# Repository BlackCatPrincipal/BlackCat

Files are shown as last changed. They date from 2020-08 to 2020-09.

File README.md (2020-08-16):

# BlackCat

Black Cat is a 3D printer project to build a fully open source 3D printed UM2 printer, and most of the components are 3D printed.

This repository contains DWG and DXF for laser cut parts, STP files and STLs for the printed parts.

Open Source with the help of [southern-dust](https://github.com/southern-dust).

#### 中文说明

BlackCat 自主设计完全开源3D打印的UM2打印机，大部分部件采用3D打印件。

这个 repo 包含用于激光切割零件的DWG和DXF文件，以及用于3D打印零件的STP和STL文件。

在 [southern-dust](https://github.com/southern-dust) 的帮助下开源。

特别的，提供作者QQ群：713105644，欢迎来交流讨论。

## License

The content of this project itself is licensed under the [Creative Commons Attribution 3.0 Unported license](https://creativecommons.org/licenses/by/3.0/), and the underlying source code used to format and display that content is licensed under the [MIT license](https://github.com/github/choosealicense.com/blob/gh-pages/LICENSE.md).

## 许可证

该项目本身的内容已根据 [Creative Commons Attribution 3.0 Unported license](https://creativecommons.org/licenses/by/3.0/) 进行了许可，用于格式化和显示该内容的基础源代码也以 [MIT license](https://github.com/github/choosealicense.com/blob/gh-pages/LICENSE.md) 进行了许可。

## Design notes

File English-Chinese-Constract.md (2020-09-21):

#### 中英文对照 English-Chinese filename constrast

##### cad(the DXF folder is the same content, but using the DXF open file format)

| Englinsh | 中文 |
| :---: | :---: |
| bottomPlate | 底板 |
| middlePlate | 中板 |
| platformBottomPlate | 平台底板 |
|  platformTopPlate | 平台上板 |

##### stl

| Englinsh | 中文 |
| :---: | :---: |
| bottomPlate | 底盘 |
| topPlate | 上盖 |
| back-Pillar | 立柱1 |
| front-Pillar | 立柱2 |
| e3d-Holder-Back | e3d支架1 |
| e3d-Holder-Front | e3d支架2 |
| Z-Carrige | z平台滑块 |
| Z-Support |  z平台三角支架  |
| Z-Shaft-Idler-10mm | z轴10mm光轴挡板 |
| Z-Endstop-Mount |  z限位固定支座  |
| motor-Spacer | 电机支架 |
| shaftBearing-Belt-holder | 直线轴承同步带  |
| PartCoolingFanMount | 风扇支架 |

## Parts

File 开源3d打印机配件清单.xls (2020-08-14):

编号 | 名称 | 规格 | 单位 | 数量 | 单价 | 总价
1 | 打印件 | 机箱外壳 | g | 1000 |  |  | Printed Parts
2 | 主板 | 创客基地MKS.Gen_L V1.0加屏幕 | 个 | 1 | 144 | 144 | Motherboard |  | 1
3 | 电机 | 42*40步进电机 | 个 | 3 | 26 | 78 | NEMA 17 Steppers | 42*40 | 3
4 | 电机 | 42*34步进电机 | 个 | 1 | 13.5 | 13.5 | NEMA 17 Steppers | 42*34 | 1 | Used for extruder?
5 | 喷头 | E3DV6 | 个 | 1 | 18 | 18 | Extruder | E3DV6 | 1
6 | 亚克力 | 285*285mm | 个 | 1 | 15 | 15 | Lasercut | 285*285mm | 1
7 | 亚克力 | 275*275mm | 个 | 1 | 15 | 15 | Lasercut | 275*275mm | 1
8 | 亚克力 | 170*180mm | 个 | 2 | 10 | 20 | Lasercut | 170*180mm | 2
9 | 限位开关 | Ultimaker2限位开关长脚 | 个 | 3 | 3 | 9 | Endstop | Mechanical Endstop | 3
10 | z轴光轴 | Φ10*320 | 根 | 2 | 7.5 | 15 | Z axis Shafts | Φ10*320 | 2
11 | x轴光轴 | Φ8*270 | 根 | 2 | 6 | 12 | X axis Shafts | Φ8*270 | 2
12 | y轴光轴 | Φ8*285 | 根 | 2 | 6 | 12 | Y axis Shafts | Φ8*285 | 2
13 | x轴十字轴 | Φ6*240 | 根 | 1 | 4.5 | 4.5 | X axis Center Shafts | Φ6*240 | 1
14 | y轴十字轴 | Φ6*225 | 根 | 1 | 4.5 | 4.5 | Y axis Center Shafts | Φ6*225 | 1
15 | 直线法兰轴承 | Φ10 | 个 | 2 | 8.45 | 16.9 | Z Shaft Flange Bearing | Φ10 | 2
16 | 散热风扇 | 30mm*30mm | 个 | 1 | 4 | 4 | fan | 30mm*30mm | 1
17 | 尼龙垫柱 | 8*2 | 个 | 8 | 0.15 | 1.2
18 | 尼龙垫柱 | 8*5 | 个 | 7 | 0.08 | 0.56
19 | 同步轮 | 2GT-20-6 | 个 | 2 | 5 | 10 | GT2 Pulley | 2GT-20-6 | 2
20 | 同步轮 | 2GT-20-8 | 个 | 8 | 7 | 56 | GT2 Pulley | 2GT-20-8 | 8
21 | 同步轮 | 2GT-20-8双头 | 个 | 1 | 9.5 | 9.5 | GT2 Pulley | 2GT-20-8 2sides | 1
22 | 弹簧 | Φ8*15 | 个 | 4 | 0.8 | 3.2
23 | 联轴器 | Φ6转Φ8铝合金联轴器 | 个 | 1 | 1.1 | 1.1 | Z Coupler | Φ6toΦ8 | 1
24 | 丝杆 | 8*270mm | 个 | 1 | 10 | 10 | Z Leadscrew/nut | 8*270mm
25 | 同步带 | 2GT闭环同步带500mm | 个 | 2 | 11.66 | 23.32 | GT2 Belt | 500mm | 1
26 | 开关 | 20mm船型开关 | 个 | 1 | 2.1 | 2.1 | Power Switch | 20mm | 1
27 | 轴承 | f688zz | 个 | 8 | 2.5 | 20 | Bearing | f688zz | 8
28 | 同步带 | 2GT同步带450mm | 个 | 4 | 1.2 | 4.8 | GT2 Belt | 450mm | 4
29 | 电源 | 5.5mmDC直流插头母头 | 个 | 1 | 3.2 | 3.2 | Power Supply
30 | 挤出机 | 泰坦远程挤出机 | 个 | 1 | 21 | 21 | Extruder | Titan remote | 1
31 | 直线轴承 | LM8UU | 个 | 4 | 2 | 8 | Shaft Bearing | LM8UU | 4
32 | 调平螺母 | m3蝶形螺母 | 个 | 4 | 1.3 | 5.2 | Nuts | M3 | 4
33 | 直线轴承 | LM6LUU | 个 | 2 | 5.5 | 11 | Shaft Bearing | LM6LUU | 2
 |  |  |  |  |  | 571.58
清单仅供参考

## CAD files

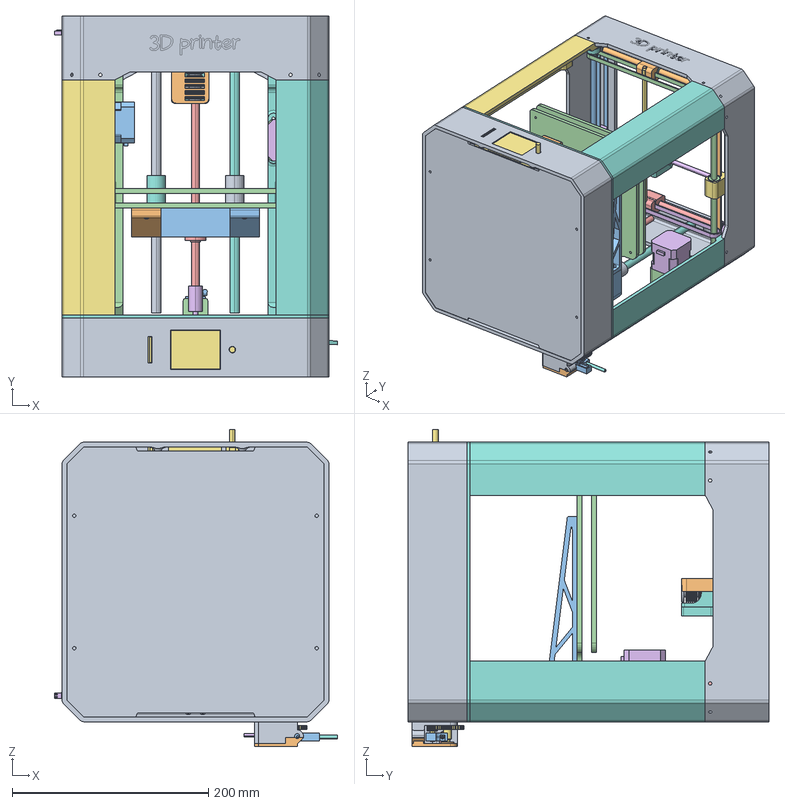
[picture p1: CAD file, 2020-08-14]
BlackCat.FCStd
288.5 x 368.0 x 323.2 mm
topPlate
GT2-Belt001
NEMA17Steppers001
back-Pillar001
GT2-Belt002
NEMA17Steppers002
front-Pillar001
front-Pillar002
bottomPlate
X-Shaft8mm001
Y-Shaft8mm001
Y-Shaft8mm002
X-Shaft8mm002
X-CenterShaftsΦ6*240
Y-CenterShaftsΦ6*225
e3d-Holder-Back
e3d-v6-hotend
e3d-Holder-Front
Z-Carrige
Y-Endstop
f688zz008
X-Endstop
LCD-SmartController
lmk10mm0002
lmk10mm001
Z-Support001
Z-Support002
platformBottomPlate
GT2-Pulley20mm001
GT2-Pulley20mm002
f688zz001
f688zz002
f688zz003
f688zz004
f688zz005
f688zz006
f688zz007
GT2-Pulley20mm003
GT2-Pulley20mm004
GT2-Pulley20mm005
GT2-Pulley20mm006
GT2-Belt450mm003
GT2-Belt450mm001
GT2-Belt450mm002
2GT-20-8 2sides
NEMA17Steppers004
NEMA17Steppers003
Z-Shaft10mm001
Z-Shaft10mm002
Z-Screw
Z-Endstop
Z-Endstop-Mount
Z-LeadscrewT8*270mm
GT2-Belt450mm004
GT2-Pulley20mm007
back-Pillar002
bottomPlate001
shaftBearing-Belt-holder004
LM6LUU002
LM8UU004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

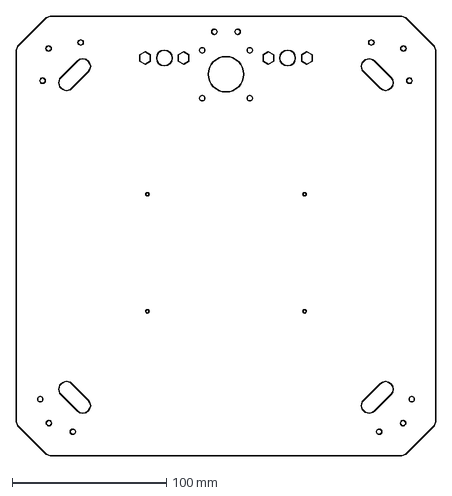
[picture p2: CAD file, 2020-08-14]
Lasercut/DXF/中板.dxf
272.0 x 285.0 mm

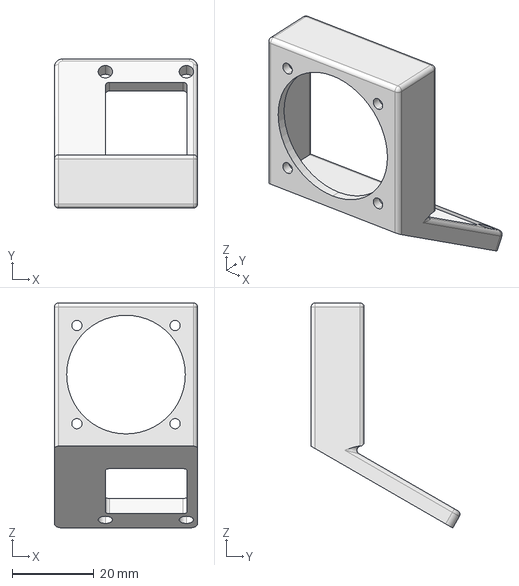
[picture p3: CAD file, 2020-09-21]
Printed-Parts/PartCoolingFanMount.FCStd
35.0 x 36.4 x 55.0 mm

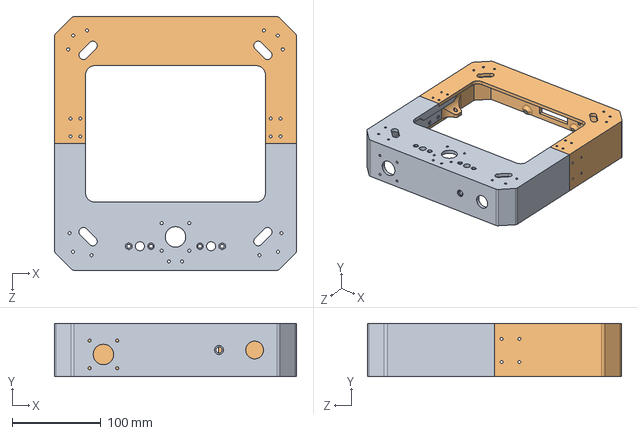
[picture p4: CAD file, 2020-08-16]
Printed-Parts/step/bottomPlate-split.step
272.0 x 60.0 x 285.0 mm
菁攫1
菁攫2

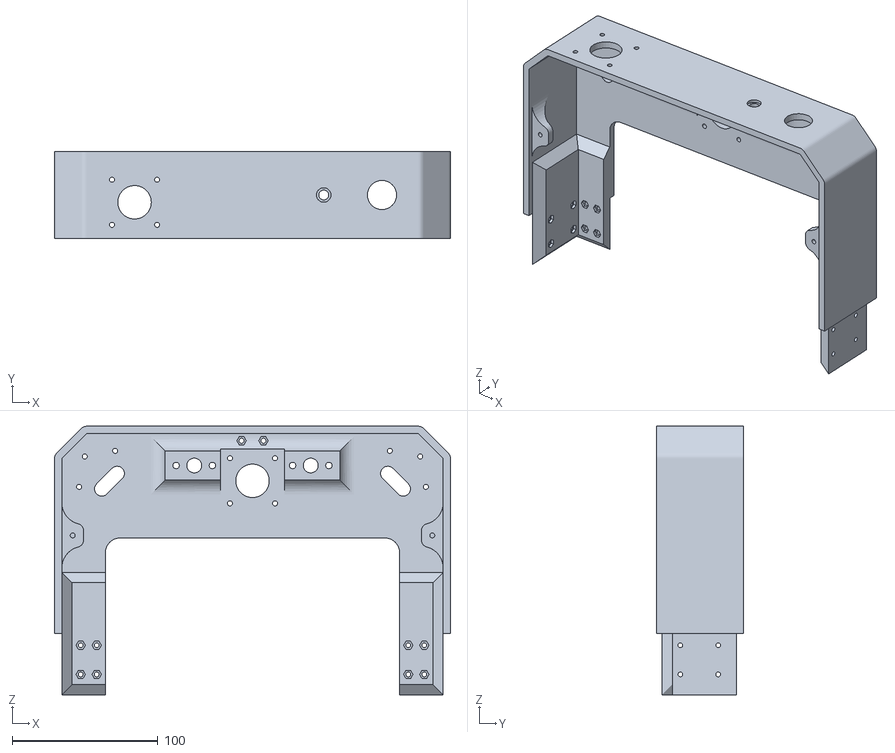
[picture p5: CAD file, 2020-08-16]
Printed-Parts/stl/bottomPlate-split-back.STL
272.0 x 60.0 x 184.5

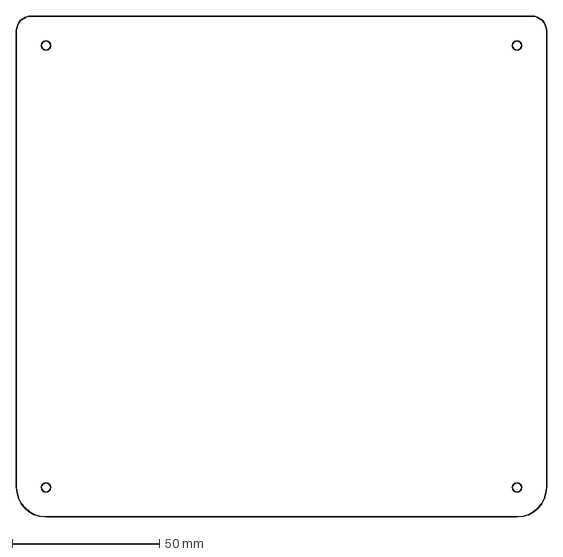
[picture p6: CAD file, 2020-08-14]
Lasercut/DXF/平台上板.dxf
180.0 x 170.0 mm

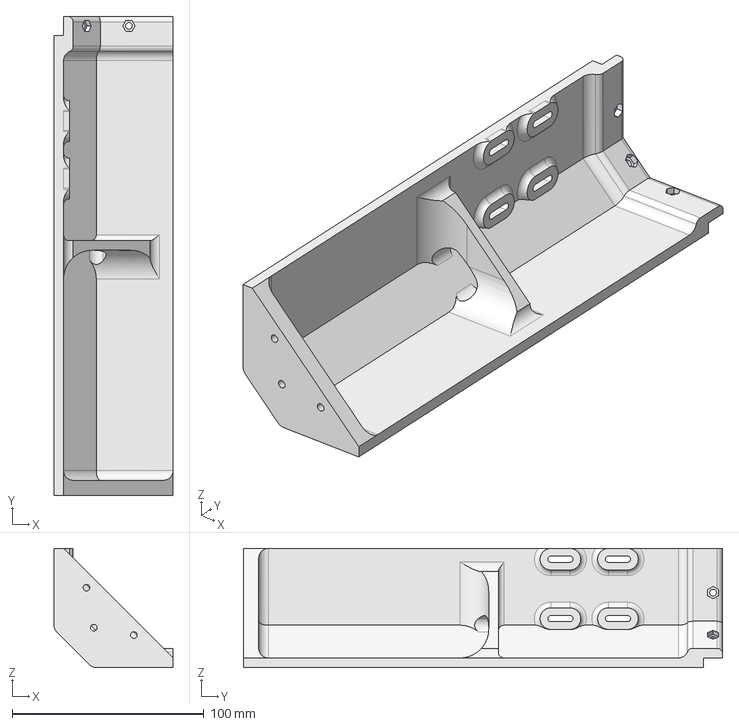
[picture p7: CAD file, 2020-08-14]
Printed-Parts/step/back-Pillar.step
62.1 x 250.0 x 62.1 mm

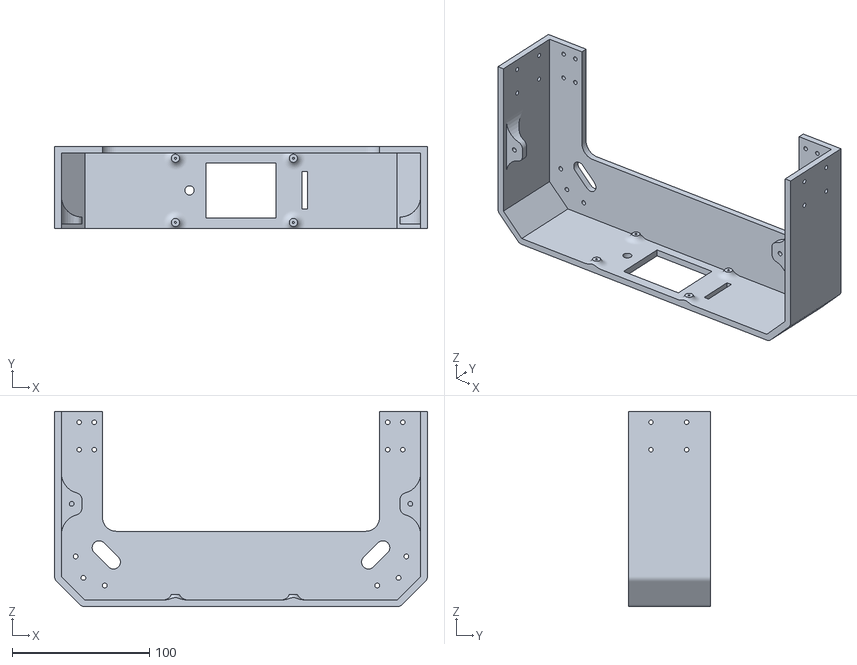
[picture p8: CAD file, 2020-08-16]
Printed-Parts/stl/bottomPlate-split-front.STL
272.0 x 60.0 x 142.5

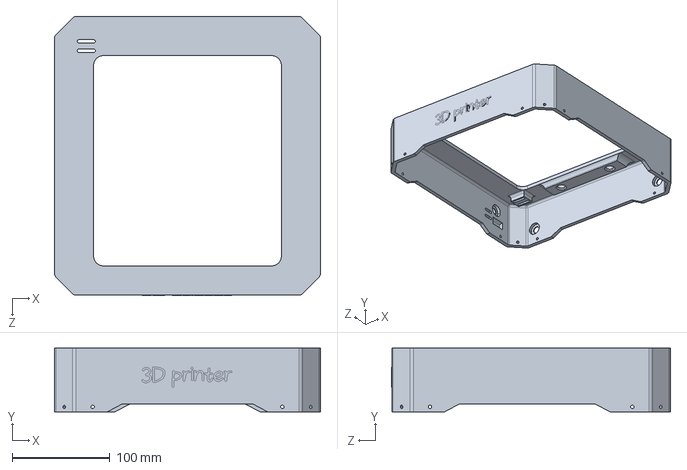
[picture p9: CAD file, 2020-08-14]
Printed-Parts/step/topPlate.step
272.0 x 65.0 x 285.3 mm

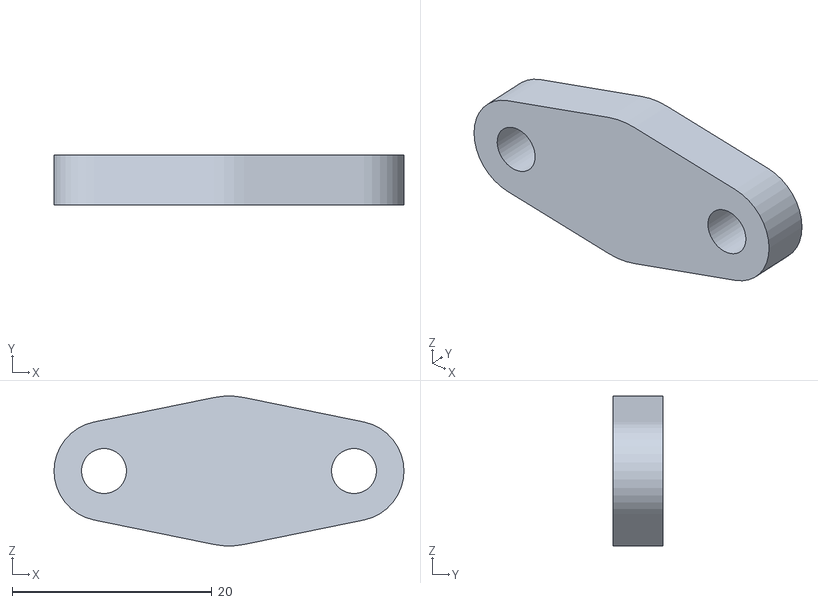
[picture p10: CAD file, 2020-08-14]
Printed-Parts/stl/z轴10mm光轴挡板.STL
35.0 x 5.00 x 15.0

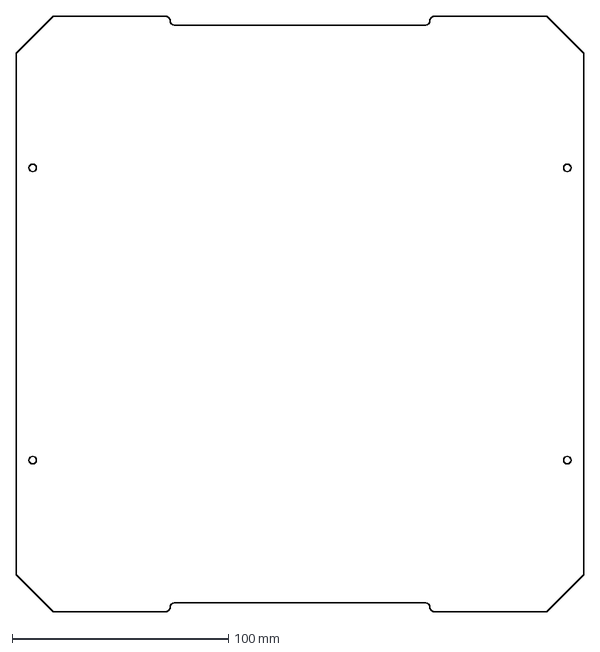
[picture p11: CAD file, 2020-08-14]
Lasercut/DXF/bottomPlate.dxf
262.0 x 275.0 mm

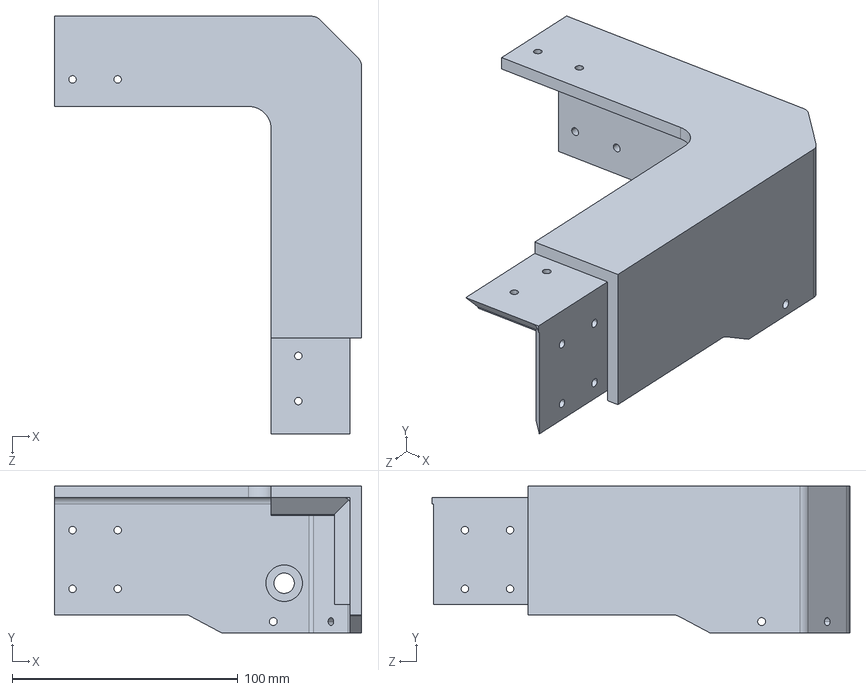
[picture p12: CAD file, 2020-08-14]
Printed-Parts/step/topPlate-split-back-right.step
136.0 x 65.0 x 185.0 mm

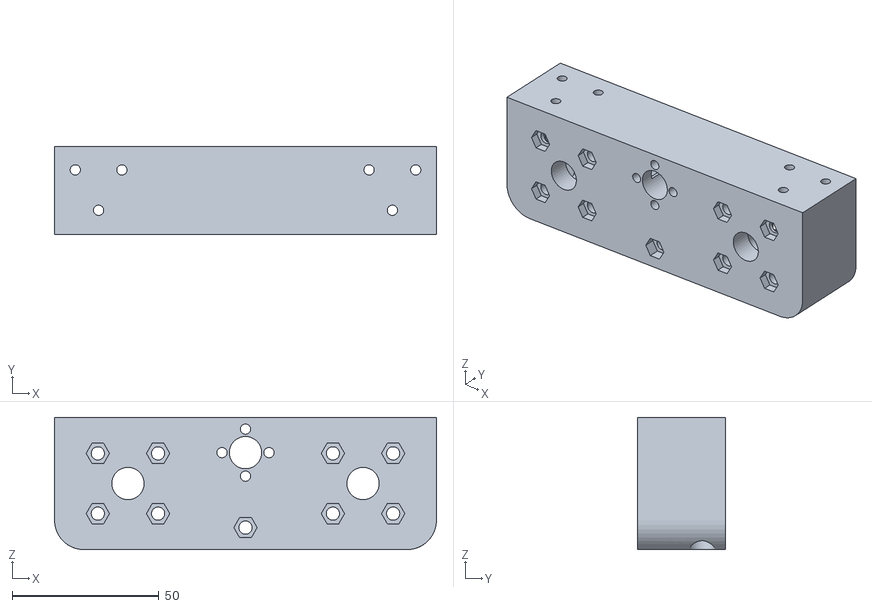
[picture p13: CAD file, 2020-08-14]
Printed-Parts/stl/z平台滑块.STL
130.0 x 30.0 x 45.0

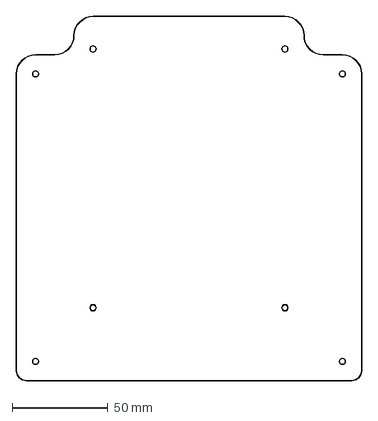
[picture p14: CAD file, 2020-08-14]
Lasercut/DXF/platformBottomPlate.dxf
180.0 x 190.0 mm

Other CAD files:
Printed-Parts/step/motor-Spacer.step
Printed-Parts/stl/z限位固定支座.STL
Lasercut/DWG/bottomPlate.DWG
Lasercut/DWG/middlePlate.DWG
Lasercut/DWG/platformBottomPlate.DWG
Lasercut/DWG/platformTopPlate.DWG
Lasercut/DWG/中板.DWG
Lasercut/DWG/平台上板.DWG
Lasercut/DWG/平台底板.DWG
Lasercut/DWG/底板.DWG
Printed-Parts/PartCoolingFanMount.STL
Printed-Parts/step/Z-Carrige.step
Printed-Parts/step/Z-Endstop-Mount.step
Printed-Parts/step/Z-Shaft-Idler-10mm.step
Printed-Parts/step/Z-Support.step
Printed-Parts/step/bottomPlate.step
Printed-Parts/step/e3d-Holder-Back.step
Printed-Parts/step/e3d-Holder-Front.step
Printed-Parts/step/front-Pillar.step
Printed-Parts/step/shaftBearing-Belt-holder.step
Printed-Parts/step/topPlate-split-back-left.step
Printed-Parts/step/topPlate-split-front-left.step
Printed-Parts/step/topPlate-split-front-right.step
Printed-Parts/stl/Z-Endstop-Mount.STL
Printed-Parts/stl/Z-Support.STL
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

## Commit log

2020-08-16 update README & add splited top&bottom Plate
    [bottomPlate-split-back.STL, bottomPlate-split-front.STL, bottomPlate-split.step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]
2020-09-21 add part cooling fan mount
    [PartCoolingFanMount.FCStd, PartCoolingFanMount.STL]
